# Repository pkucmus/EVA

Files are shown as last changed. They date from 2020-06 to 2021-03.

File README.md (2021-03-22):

# EVA 1 is deprecated since 2020-12-31 
# go to [EVA 2](https://main.eva-3d.page/) for the new thing

# EVA MGN Carriage Platform

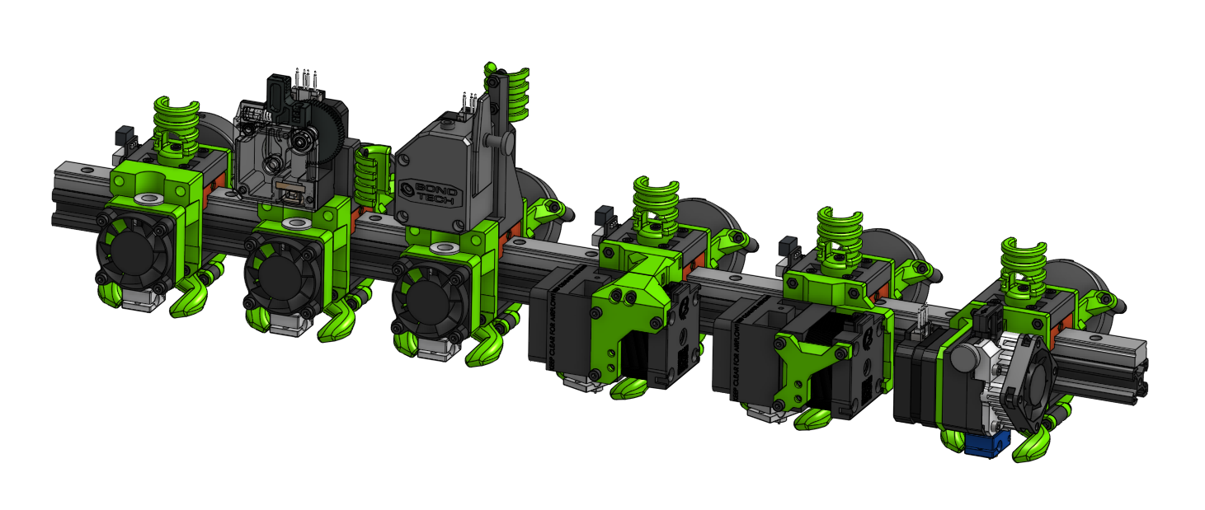
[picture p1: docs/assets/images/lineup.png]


I present to you the EVA carriage platform - easy to mount, remix and use MGN carriages for different Hotend assemblies.

They work great with the [Rat Rig V-core Pro](https://www.ratrig.com/3d-printing-cnc/3d-printer-kits/complete-kits/rat-rig-v-core-pro-linear-rail-701.html) "Easy mod" I created: https://github.com/pkucmus/Easy-Mod

A rather poor attempt to talk about those: https://www.youtube.com/playlist?list=PLR8LTCniA766Mg1a88iF8xhOlvZR-Rc3A

## Instructions

Visit the [project page](https://pkucmus.github.io/EVA/) for instructions and more information.

## Contribution

If you want to help with testing - please grab a carriage and report your findings as an [issue](https://github.com/pkucmus/EVA/issues) - please include pictures, videos and your opinion.

If you see anything missing from the Instructions - please file an [issue](https://github.com/pkucmus/EVA/issues).

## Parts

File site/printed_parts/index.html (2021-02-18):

Part | Link
bottom_mgn15_short_duct | GitHub (https://github.com/pkucmus/EVA/tree/master/docs/media/stls/bottom_mgn15_short_duct.stl)
Duct v2 Straight Risen | GitHub (https://github.com/pkucmus/EVA/tree/master/docs/media/stls/duct-v2-straight-risen.stl)
back_corexy_90deg | GitHub (https://github.com/pkucmus/EVA/tree/master/docs/media/stls/back_corexy_90deg.stl)
tension_slider_9mm_belt_M5_mirror | GitHub (https://github.com/pkucmus/EVA/tree/master/docs/media/stls/tension_slider_9mm_belt_m5_mirror.stl)
tension_slider_9mm_belt_M5 | GitHub (https://github.com/pkucmus/EVA/tree/master/docs/media/stls/tension_slider_9mm_belt_m5.stl)
cable_side | GitHub (https://github.com/pkucmus/EVA/tree/master/docs/media/stls/cable_side.stl)
unversal_cable_mount | GitHub (https://github.com/pkucmus/EVA/tree/master/docs/media/stls/unversal_cable_mount.stl)
top_mgn15_raw | GitHub (https://github.com/pkucmus/EVA/tree/master/docs/media/stls/top_mgn15_raw.stl)
face_v6 | GitHub (https://github.com/pkucmus/EVA/tree/master/docs/media/stls/face_v6.stl)
face_v6_40mm_fan | GitHub (https://github.com/pkucmus/EVA/tree/master/docs/media/stls/face_v6_40mm_fan.stl)
face_mosquito | GitHub (https://github.com/pkucmus/EVA/tree/master/docs/media/stls/face_mosquito.stl)
mosquito_front | GitHub (https://github.com/pkucmus/EVA/tree/master/docs/media/stls/mosquito_front.stl)
back_cartesian | GitHub (https://github.com/pkucmus/EVA/tree/master/docs/media/stls/back_cartesian.stl)
tension_slider_6mm_belt_M3 | GitHub (https://github.com/pkucmus/EVA/tree/master/docs/media/stls/tension_slider_6mm_belt_m3.stl)
cartesian_cable_fin | GitHub (https://github.com/pkucmus/EVA/tree/master/docs/media/stls/cartesian_cable_fin.stl)
bottom_mgn12_short_duct | GitHub (https://github.com/pkucmus/EVA/tree/master/docs/media/stls/bottom_mgn12_short_duct.stl)
top_mgn12_raw | GitHub (https://github.com/pkucmus/EVA/tree/master/docs/media/stls/top_mgn12_raw.stl)
face_titan | GitHub (https://github.com/pkucmus/EVA/tree/master/docs/media/stls/face_titan.stl)
face_mosquito_titan | GitHub (https://github.com/pkucmus/EVA/tree/master/docs/media/stls/face_mosquito_titan.stl)
top_mgn15_bmg | GitHub (https://github.com/pkucmus/EVA/tree/master/docs/media/stls/top_mgn15_bmg.stl)
top_mgn12_bmg | GitHub (https://github.com/pkucmus/EVA/tree/master/docs/media/stls/top_mgn12_bmg.stl)
bottom_mgn15_long_duct | GitHub (https://github.com/pkucmus/EVA/tree/master/docs/media/stls/bottom_mgn15_long_duct.stl)
face_aero | GitHub (https://github.com/pkucmus/EVA/tree/master/docs/media/stls/face_aero.stl)
face_aero_support | GitHub (https://github.com/pkucmus/EVA/tree/master/docs/media/stls/face_aero_support.stl)
bottom_mgn12_long_duct | GitHub (https://github.com/pkucmus/EVA/tree/master/docs/media/stls/bottom_mgn12_long_duct.stl)
Duct v2 Angled 20deg Risen | GitHub (https://github.com/pkucmus/EVA/tree/master/docs/media/stls/duct-v2-angled-20deg-risen.stl)
face_hemera | GitHub (https://github.com/pkucmus/EVA/tree/master/docs/media/stls/face_hemera.stl)
face_hemera_front | GitHub (https://github.com/pkucmus/EVA/tree/master/docs/media/stls/face_hemera_front.stl)
Duct v2 Volcano Straight Risen | GitHub (https://github.com/pkucmus/EVA/tree/master/docs/media/stls/Duct_v2_Volcano_Configurable_-_Duct_v2_Volcano_Straight_Risen.stl)
Duct v2 Volcano Angled Risen | GitHub (https://github.com/pkucmus/EVA/tree/master/docs/media/stls/Duct_v2_Volcano_Configurable_-_Duct_v2_Volcano_Angled_20deg_Risen.stl)
Back IDEX X1 | GitHub (https://github.com/pkucmus/EVA/tree/master/docs/media/stls/Back_IDEX_-_back_idex_x1.stl)
Back IDEX X2 | GitHub (https://github.com/pkucmus/EVA/tree/master/docs/media/stls/Back_IDEX_-_back_idex_x2.stl)

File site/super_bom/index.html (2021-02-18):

Name | Qty | Type | Link
bottom_mgn15_short_duct | 1.0 | printed | GitHub (https://github.com/pkucmus/EVA/tree/master/docs/media/stls/bottom_mgn15_short_duct.stl)
DIN 912 M3 20 mm | 5.0 | hardware
Duct v2 Straight Risen | 1.0 | printed | GitHub (https://github.com/pkucmus/EVA/tree/master/docs/media/stls/duct-v2-straight-risen.stl)
M3 Hex nut | 20.0 | hardware
back_corexy_90deg | 1.0 | printed | GitHub (https://github.com/pkucmus/EVA/tree/master/docs/media/stls/back_corexy_90deg.stl)
DIN 912 M5 35 mm | 2.0 | hardware
tension_slider_9mm_belt_M5_mirror | 1.0 | printed | GitHub (https://github.com/pkucmus/EVA/tree/master/docs/media/stls/tension_slider_9mm_belt_m5_mirror.stl)
tension_slider_9mm_belt_M5 | 1.0 | printed | GitHub (https://github.com/pkucmus/EVA/tree/master/docs/media/stls/tension_slider_9mm_belt_m5.stl)
5015 fan | 1.0 | hardware
M5 Hex nut | 2.0 | hardware
cable_side | 1.0 | printed | GitHub (https://github.com/pkucmus/EVA/tree/master/docs/media/stls/cable_side.stl)
unversal_cable_mount | 1.0 | printed | GitHub (https://github.com/pkucmus/EVA/tree/master/docs/media/stls/unversal_cable_mount.stl)
DIN 912 M3 10 mm | 10.0 | hardware
DIN 912 M3 12 mm | 9.0 | hardware
top_mgn15_raw | 1.0 | printed | GitHub (https://github.com/pkucmus/EVA/tree/master/docs/media/stls/top_mgn15_raw.stl)
face_v6 | 1.0 | printed | GitHub (https://github.com/pkucmus/EVA/tree/master/docs/media/stls/face_v6.stl)
DIN 912 M3 40 mm | 4.0 | hardware
face_v6_40mm_fan | 1.0 | printed | GitHub (https://github.com/pkucmus/EVA/tree/master/docs/media/stls/face_v6_40mm_fan.stl)
4010 FAN | 1.0 | hardware
V6-175-SINK | 1.0 | hardware
V6-300-BREAK | 1.0 | hardware
V6-BLOCK-CARTRIDGE | 1.0 | hardware
V6-NOZZLE-ALL | 1.0 | hardware
SOCK | 1.0 | hardware
DIN 912 M3 35 mm | 7.0 | hardware
mosquito | 1.0 | hardware
25mm fan | 1.0 | hardware
DIN 912 M3 25 mm | 3.0 | hardware
DIN 912 M2.5 12 mm | 2.0 | hardware
face_mosquito | 1.0 | printed | GitHub (https://github.com/pkucmus/EVA/tree/master/docs/media/stls/face_mosquito.stl)
mosquito_front | 1.0 | printed | GitHub (https://github.com/pkucmus/EVA/tree/master/docs/media/stls/mosquito_front.stl)
back_cartesian | 1.0 | printed | GitHub (https://github.com/pkucmus/EVA/tree/master/docs/media/stls/back_cartesian.stl)
tension_slider_6mm_belt_M3 | 1.0 | printed | GitHub (https://github.com/pkucmus/EVA/tree/master/docs/media/stls/tension_slider_6mm_belt_m3.stl)
cartesian_cable_fin | 1.0 | printed | GitHub (https://github.com/pkucmus/EVA/tree/master/docs/media/stls/cartesian_cable_fin.stl)
DIN 912 M3 30 mm | 2.0 | hardware
bottom_mgn12_short_duct | 1.0 | printed | GitHub (https://github.com/pkucmus/EVA/tree/master/docs/media/stls/bottom_mgn12_short_duct.stl)
DIN 912 M3 16 mm | 2.0 | hardware
top_mgn12_raw | 1.0 | printed | GitHub (https://github.com/pkucmus/EVA/tree/master/docs/media/stls/top_mgn12_raw.stl)
face_titan | 1.0 | printed | GitHub (https://github.com/pkucmus/EVA/tree/master/docs/media/stls/face_titan.stl)
PTFE Tube 73.6 millimeter | 1.0 | hardware
PTFE Tube 57 millimeter | 1.0 | hardware
face_mosquito_titan | 1.0 | printed | GitHub (https://github.com/pkucmus/EVA/tree/master/docs/media/stls/face_mosquito_titan.stl)
top_mgn15_bmg | 1.0 | printed | GitHub (https://github.com/pkucmus/EVA/tree/master/docs/media/stls/top_mgn15_bmg.stl)
BMG-M_Extruder | 1.0 | hardware
top_mgn12_bmg | 1.0 | printed | GitHub (https://github.com/pkucmus/EVA/tree/master/docs/media/stls/top_mgn12_bmg.stl)
bottom_mgn15_long_duct | 1.0 | printed | GitHub (https://github.com/pkucmus/EVA/tree/master/docs/media/stls/bottom_mgn15_long_duct.stl)
face_aero | 1.0 | printed | GitHub (https://github.com/pkucmus/EVA/tree/master/docs/media/stls/face_aero.stl)
face_aero_support | 1.0 | printed | GitHub (https://github.com/pkucmus/EVA/tree/master/docs/media/stls/face_aero_support.stl)
DIN 912 M3 8 mm | 5.0 | hardware
E3Dv6 Break | 1.0 | hardware
E3Dv6 Block | 1.0 | hardware
E3Dv6 Nozzle 0.4 | 1.0 | hardware
bottom_mgn12_long_duct | 1.0 | printed | GitHub (https://github.com/pkucmus/EVA/tree/master/docs/media/stls/bottom_mgn12_long_duct.stl)
Duct v2 Angled 20deg Risen | 1.0 | printed | GitHub (https://github.com/pkucmus/EVA/tree/master/docs/media/stls/duct-v2-angled-20deg-risen.stl)
40x40x10 DC Fan | 1.0 | hardware
HEMERA-175-SINK_1_1_1_1 | 1.0 | hardware
HEMERA-MOTOR_1_1_1_1_1_1 | 2.0 | hardware
V6-BLOCK-CARTRIDGE_1_1_1_1_1_1 | 1.0 | hardware
V6-NOZZLE_1_1_1_1_1_1 | 1.0 | hardware
HEMERA-175-BREAK_1_1_1_1_1_1 | 1.0 | hardware
square nut thin grade b_din_Square nut DIN 562 M3 -N_1_1_1_1_1 | 5.0 | hardware
face_hemera | 1.0 | printed | GitHub (https://github.com/pkucmus/EVA/tree/master/docs/media/stls/face_hemera.stl)
face_hemera_front | 1.0 | printed | GitHub (https://github.com/pkucmus/EVA/tree/master/docs/media/stls/face_hemera_front.stl)

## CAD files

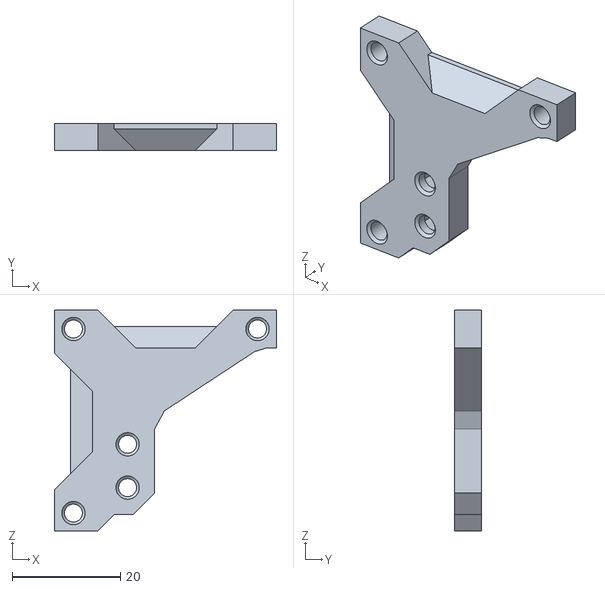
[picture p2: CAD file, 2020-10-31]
docs/media/stls/face_hemera_front.stl
41.0 x 5.00 x 40.8

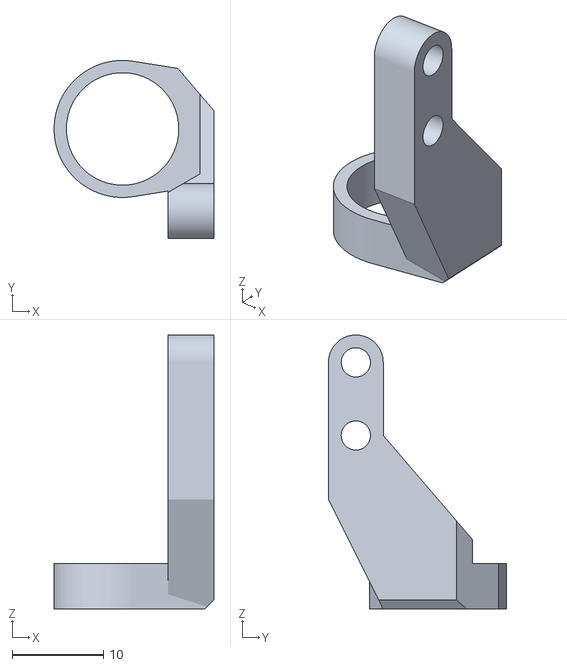
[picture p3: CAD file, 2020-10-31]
site/media/stls/probes - lj12_probe_left.stl
17.5 x 19.5 x 30.0

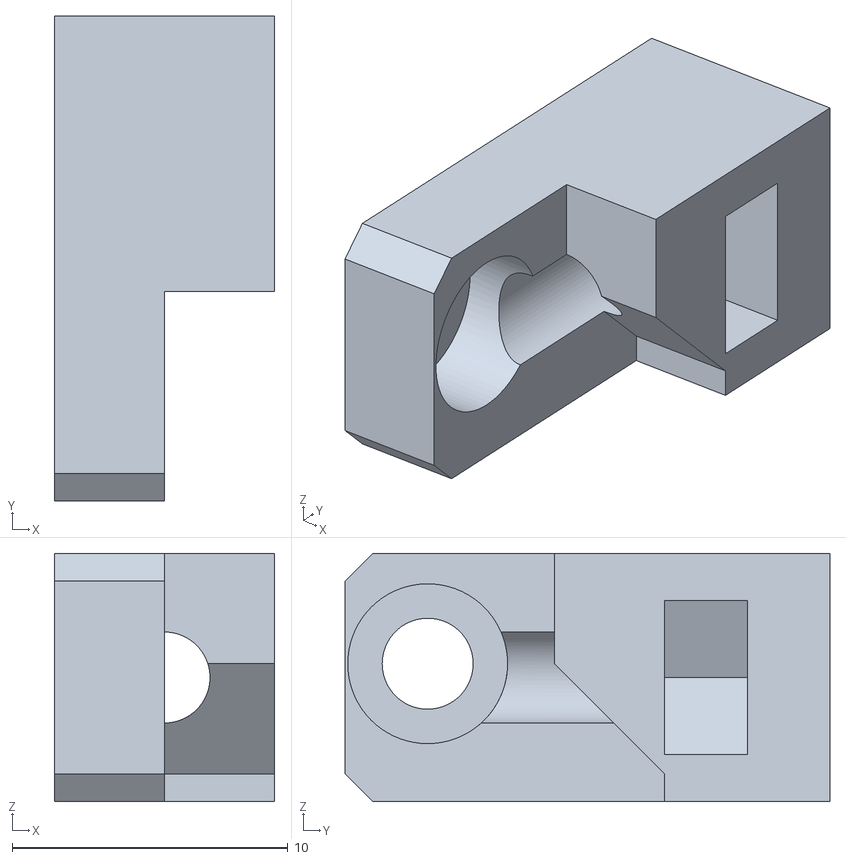
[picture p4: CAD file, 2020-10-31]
docs/media/stls/face_aero_support.stl
8.00 x 17.6 x 9.00

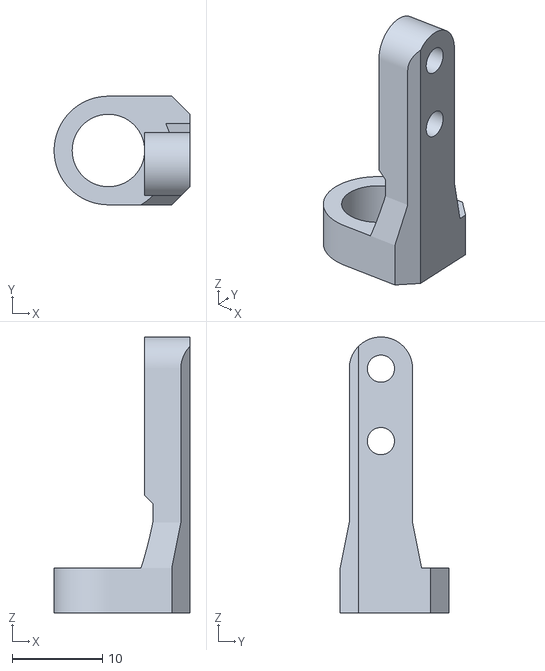
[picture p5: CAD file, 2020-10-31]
site/media/stls/probes - lj8_probe_center.stl
15.0 x 12.0 x 30.5

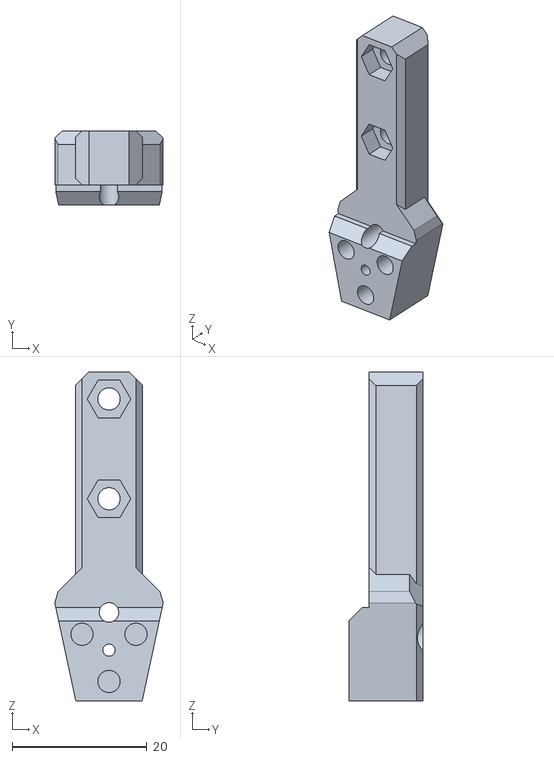
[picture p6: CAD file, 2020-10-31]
docs/media/stls/unversal_cable_mount.stl
16.1 x 11.0 x 48.8

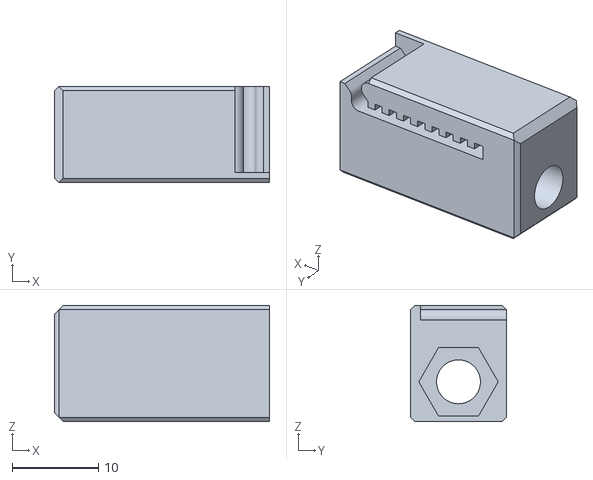
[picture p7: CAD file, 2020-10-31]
site/media/stls/tension sliders - tension_slider_9mm_belt_M5_mirror.stl
25.0 x 11.2 x 13.5

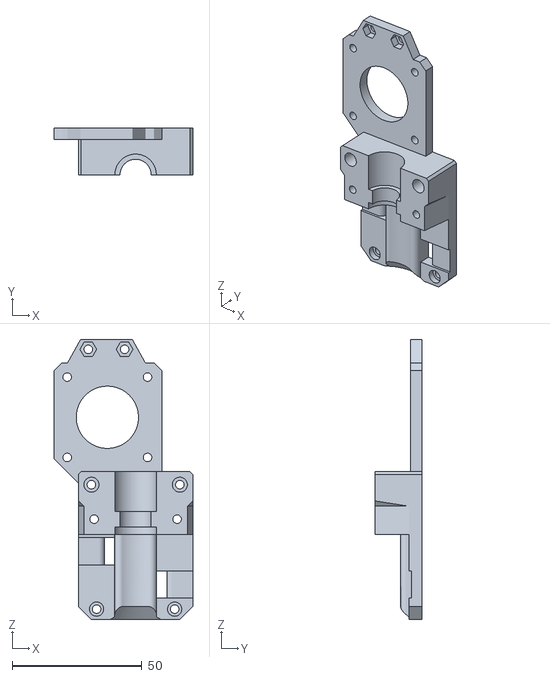
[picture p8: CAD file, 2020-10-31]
docs/media/stls/face_titan.stl
53.5 x 18.0 x 108.0

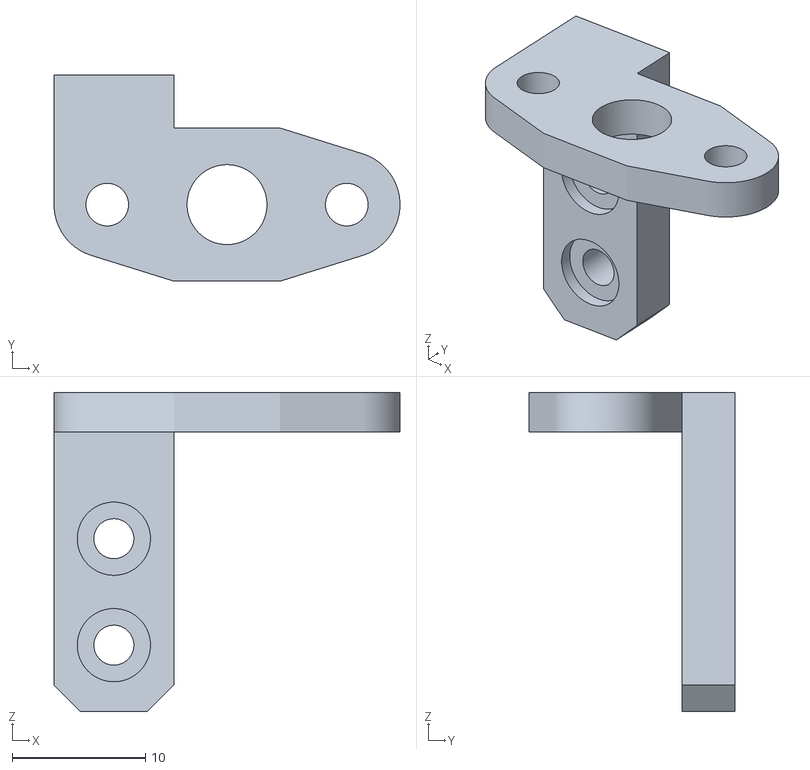
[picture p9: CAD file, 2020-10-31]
site/media/stls/probes - bl_touch_3mm.stl
26.0 x 15.5 x 24.0

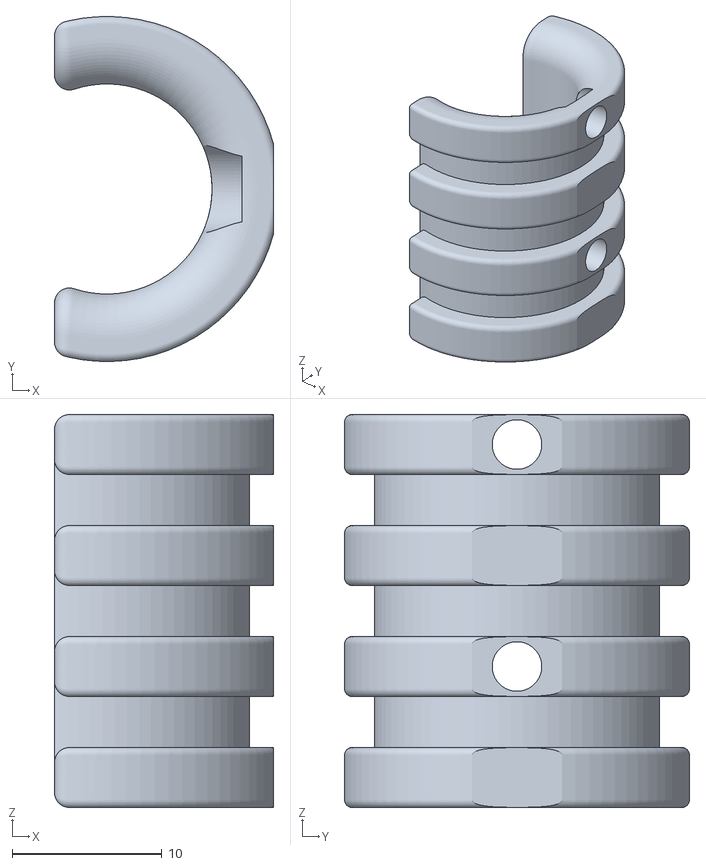
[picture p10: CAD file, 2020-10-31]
docs/media/stls/cable_side.stl
14.6 x 23.0 x 26.2

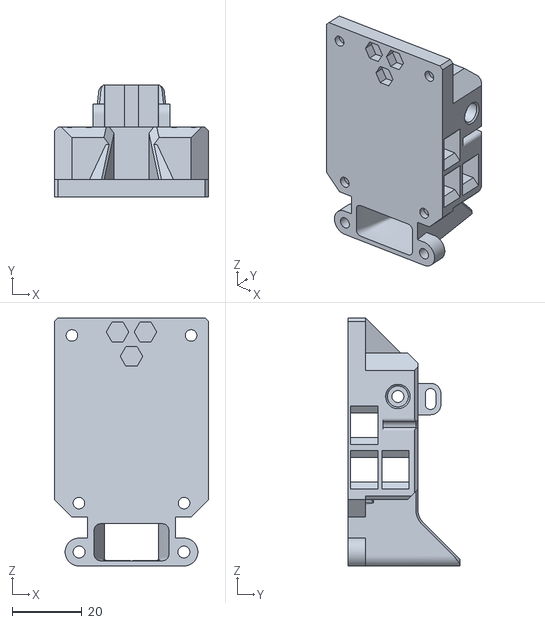
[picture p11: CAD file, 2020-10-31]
site/media/stls/Back_IDEX_-_back_idex_x2.stl
44.1 x 32.0 x 71.0

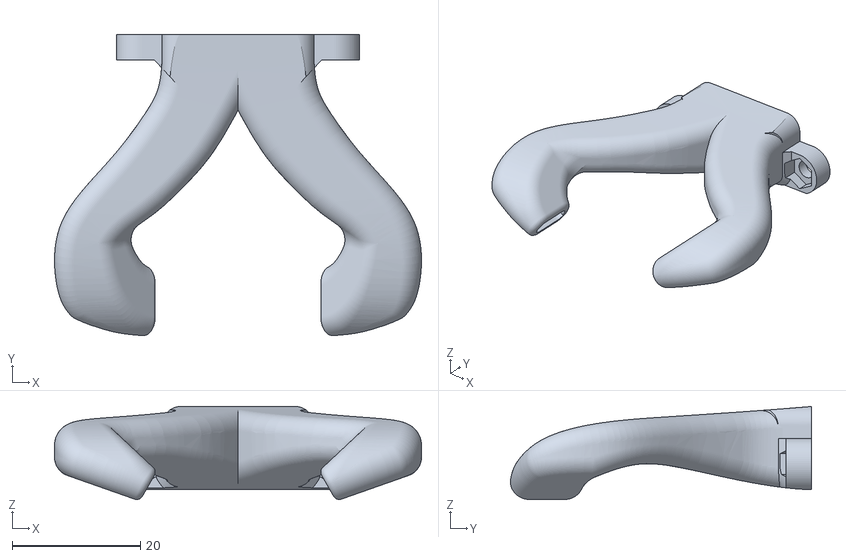
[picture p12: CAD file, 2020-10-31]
docs/media/stls/duct-v2-straight-risen.stl
57.3 x 47.0 x 14.5

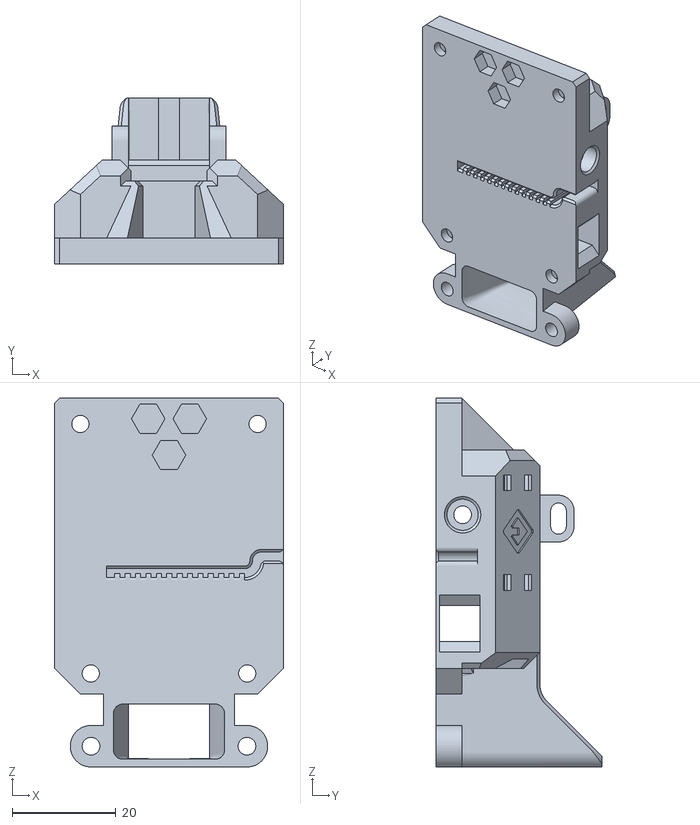
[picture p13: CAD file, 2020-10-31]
docs/media/stls/back_cartesian.stl
44.1 x 32.0 x 71.0

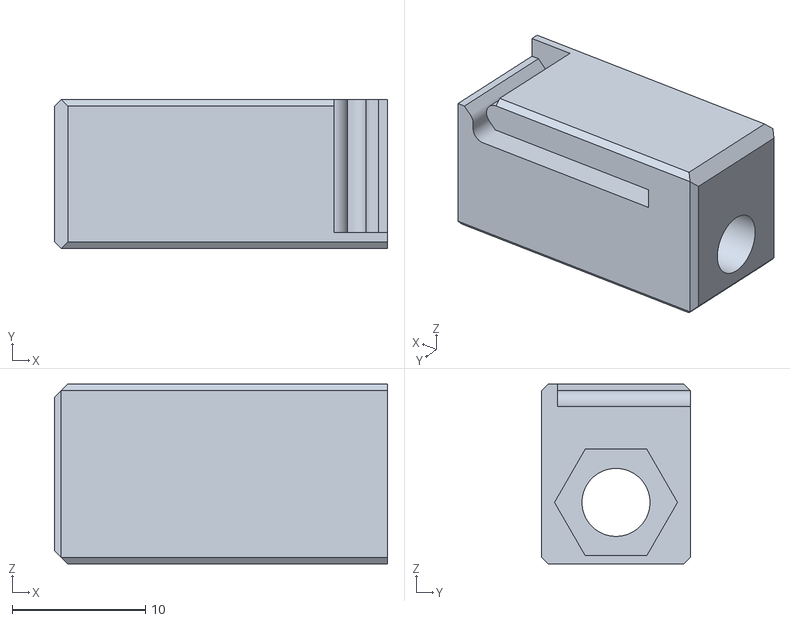
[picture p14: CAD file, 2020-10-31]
site/media/stls/tension sliders - tension_slider_9mm_belt_M5_flip_mirror.stl
25.0 x 11.2 x 13.5

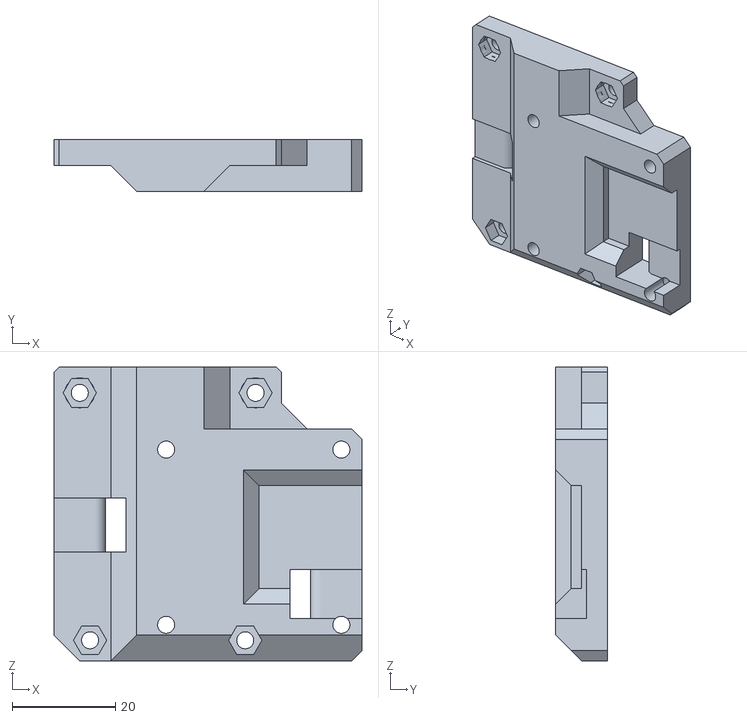
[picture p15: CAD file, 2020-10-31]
docs/media/stls/face_hemera.stl
59.8 x 10.0 x 57.0

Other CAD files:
site/media/stls/tension sliders - tension_slider_9mm_belt_M5.stl
site/media/stls/Back_IDEX_-_back_idex_x1.stl
docs/media/stls/bottom_mgn15_long_duct.stl
site/media/stls/probes - lj8_probe_right.stl
docs/media/stls/back_corexy_90deg.stl
docs/media/stls/bottom_mgn12_long_duct.stl
docs/media/stls/bottom_mgn12_short_duct.stl
docs/media/stls/bottom_mgn15_short_duct.stl
docs/media/stls/cartesian_cable_fin.stl
docs/media/stls/duct-v2-angled-20deg-risen.stl
docs/media/stls/face_aero.stl
docs/media/stls/face_mosquito.stl
docs/media/stls/face_mosquito_titan.stl
docs/media/stls/face_v6.stl
docs/media/stls/face_v6_40mm_fan.stl
docs/media/stls/mosquito_front.stl
docs/media/stls/tension_slider_6mm_belt_m3.stl
docs/media/stls/tension_slider_9mm_belt_m5.stl
docs/media/stls/tension_slider_9mm_belt_m5_mirror.stl
docs/media/stls/top_mgn12_bmg.stl
docs/media/stls/top_mgn12_raw.stl
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

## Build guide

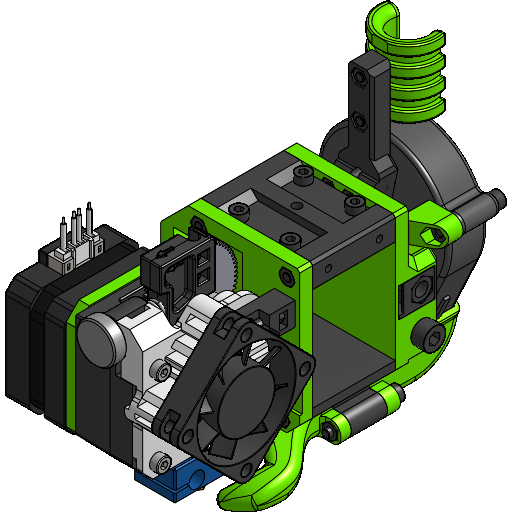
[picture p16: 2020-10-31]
site/media/assemblies/44f6d805bfa7d15742b3ac6fList_SNSHSCw9hkRS4VDefaultList_AYF7J5g18MUh8SDefault.png

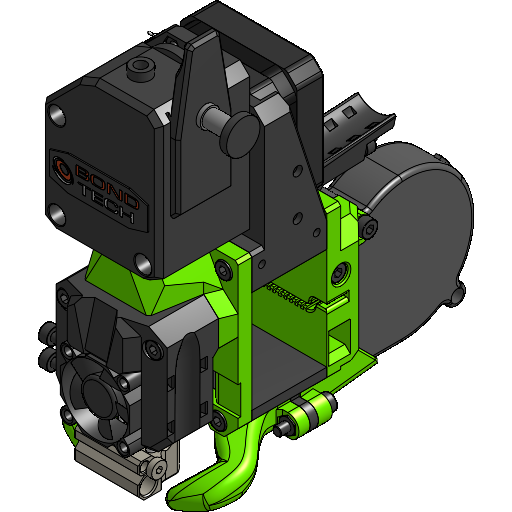
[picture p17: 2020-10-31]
docs/media/assemblies/e089ef52b1a648887b30ed21List_tcI8zlLYtHoV29MGN12List_6rEL4KZ3PThss0MosquitoLi_g8Y7Tob.png

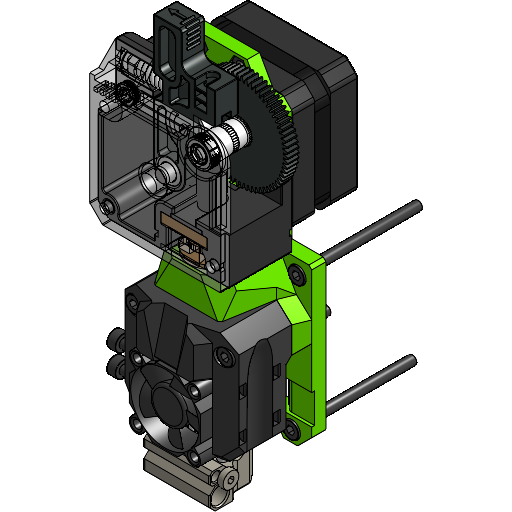
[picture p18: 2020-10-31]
docs/media/sub_assemblies/Face_Mosquito_Titan.png

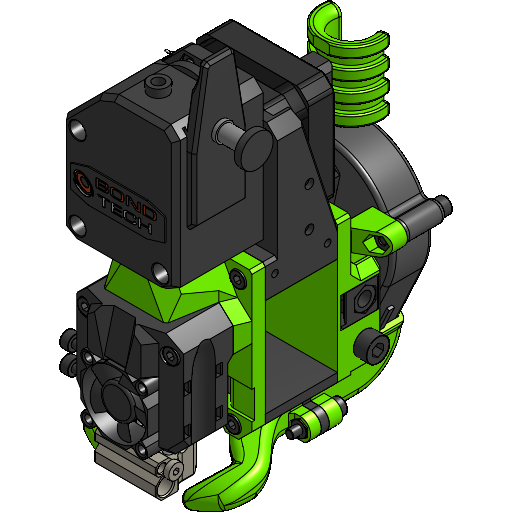
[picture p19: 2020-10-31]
docs/media/assemblies/e089ef52b1a648887b30ed21List_tcI8zlLYtHoV29MGN12List_6rEL4KZ3PThss0Mosquito_B_u0amaoS.png

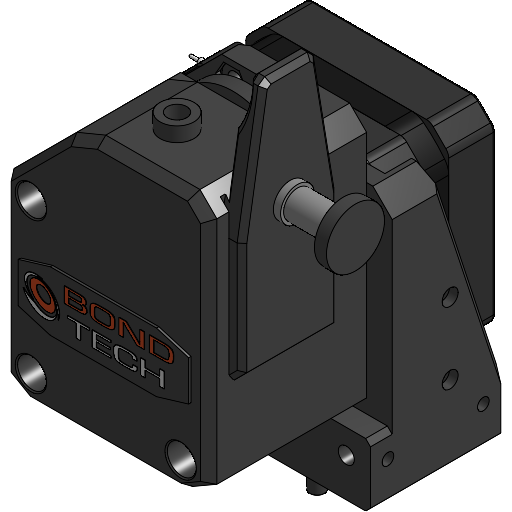
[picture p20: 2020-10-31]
site/media/sub_assemblies/Top_BMG_XyYwNrb.png

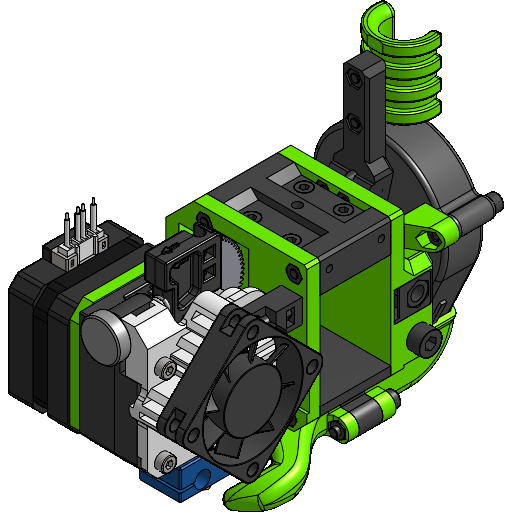
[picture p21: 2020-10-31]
docs/media/assemblies/44f6d805bfa7d15742b3ac6fList_SNSHSCw9hkRS4VMGN12List_AYF7J5g18MUh8SDefault.png

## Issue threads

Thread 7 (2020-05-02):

Anycubic / Creality Cartesian Mods

DavaD85, 2020-05-02:
Hi
I would like to know if is possible to have a simple mod to fit this Extruder to a cartesian printer like Chiron or Cr10, I need to have a single belt.

Thanks!

pkucmus, 2020-05-02:
We talked and there is a difficulty coming out from the belt issue CR-10 and it's derivatives has. Additionally there is not much space on the back for an EVA back belt mount.

Ideas are welcome :)

pkucmus, 2020-05-07:
I have a cartesian version in the workings but it will require a change in the belt paths on the CR-10 deriatives

pkucmus, 2020-05-10:
The cartesian version of EVA is uploaded, more information here: https://pkucmus.github.io/EVA/sub_assemblies/cartesian_back/

pkucmus, 2020-06-06:
Cartesian back is available. Different mods for different printers would need to be done as mods for those printers. There's also V-cast incoming: https://www.ratrig.com/3d-printing-cnc/3d-printer-kits/complete-kits/rat-rig-v-cast.html

Closed 2020-06-06.

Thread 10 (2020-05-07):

fandduck its lower than the nozzle

DavaD85, 2020-05-07:
I tried to print the fanduck and it's lower than the nozzle, maybe it's the abs retraction during the print of this part, it's possible to move up a little?
Thanks

DavaD85, 2020-05-07:
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

pkucmus, 2020-05-07:
I'm going to pause on this one to make sure it's not a printout issue.

pkucmus, 2020-05-27:
Do I recall correctly that we talked about it on Messenger and the issue is resolved?

PeterDavidsson, 2020-05-28:
Hi,
I do also have this problem, how did you solve this?
I have tride both versions of your horn_duct.

pkucmus, 2020-05-28:
I suppose this might be an issue with different sizes of heat blocks - there seems to be two. I guess I'll need to make one that's 2mm(?) raised.

PeterDavidsson, 2020-05-29:
That would be nice.
I also hade to remove the bottomplate distance were you mount the shroud to make airflow spot on.
But 2mm higher would be very nice.

pkucmus, 2020-05-29:
Please tell me what exactly do you mean by "remove the bottomplate distance" ?

pkucmus, 2020-05-29:
I uploaded raised versions to a test branch: https://github.com/pkucmus/EVA/tree/raised_duct/stl (look for `_raised` files - it's raised 1mm (2mm seemed too much).

Please let me know if it's better so I can release it officially.

PeterDavidsson, 2020-06-02:
now the flow is spot on for me
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

pkucmus, 2020-06-06:
Fixed with 1.1.0

Closed 2020-06-06.

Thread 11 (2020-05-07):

Belt tension for sapphire plus

DavaD85, 2020-05-07:
Hi
My Sapphire plus have the belts in the opposite side and I need to mirror this part, it's possible?
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
![Uploading 20200507_222611.jpg…]()

DavaD85, 2020-05-07:
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

pkucmus, 2020-05-07:
Since we started talking about it outside of GitHub it's already done :D

https://github.com/pkucmus/EVA/blob/flipped_slider/stl/Dynamic%20-%20Slider.stl

Please let me know if it works.

DavaD85, 2020-05-08:
Hi
As you can see I need to move the belt a little
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
And the part is a little lower than the original

pkucmus, 2020-05-27:
I think we talked about it. Two things can be done here:
1. Thicken the back part to offset the belt tensioner
2. Change the XY joiner part of the printer

I'd rather opt for the later one, since there's already little space in Y on that printer.

pkucmus, 2020-06-06:
Different belt tension sliders are now available - fill support for Sapphire plus is not something I can take on. Closing this one :)

Closed 2020-06-06.

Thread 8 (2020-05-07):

Mount for BMG Aero

KipK, 2020-05-07:
Hi

Great work you did here.

I've started to make a mount for the new BMG Aero from mellow. It' a kind of a remix of a BMG with Hemera heatsink, the titan aero way.

https://www.aliexpress.com/i/4000084805415.html

I'd like to remix your fan duct on it, would you mind to share the step file ?

Thanks

Gui

pkucmus, 2020-05-07:
Thank you and Awesome! You'd like it to be a part of EVA?

The thing is that I can't guarantee that stuff will not change at this point but if you still want to give it a go I could give you the required step files (the ducts and a base face maybe?).

KipK, 2020-05-07:
Sure, whatever you have that can inspire me too. If you have the Hemera
step file too as booth have almost the same footprint

I'm almost done making a BLV mount for it that fits bltouch and 5015 blower
but I'm now stuck fitting a proper cooling duct.
I don't mind redoing it by to be more EVA lookish ;)
How the fan ducts doing is job on your setup?
I was quiet used to double 4010 blowers.

Le jeu. 7 mai 2020 à 17:21, Paweł Kucmus <notifications@github.com> a
écrit :

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

KipK, 2020-05-07:
Titan aero mount seems the nearest start  for this one. So I'd rather have this step
Here is a STL of the extruder
https://www.thingiverse.com/thing:4226245

pkucmus, 2020-05-08:
To answer the question about he fan duct - it's doing very well, I was surprised i.e. how long of a bridge I can make with it.
Here's a CFG simulation result from this week:
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

pkucmus, 2020-05-27:
Ho is it going? Do you need anything else?

KipK, 2020-05-30:
Hey.

Sorry was busy those days.
I've misthought it was for BLV mgn printer.
Tryed to modify for it and fits all my needs but finally was not satisfied
by this extruder positioning and weight. ( Not your design but this
extruder design sideways as I prefer a dual blower config.
For now I've made something else, but will probably work on it back later

Le mer. 27 mai 2020 à 09:41, Paweł Kucmus <notifications@github.com> a
écrit :

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

pkucmus, 2020-09-05:
Thanks, I'll close this one for now, we can always revisit the idea in the future

Closed 2020-09-05.

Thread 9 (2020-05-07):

fan problem

DavaD85, 2020-05-07:
I need to move a little down the back fan because doesn't fit in my Sapphire plus frame.

DavaD85, 2020-05-07:
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

pkucmus, 2020-05-09:
I made 4 more versions which total up to 5:
* 30 deg
* 45 deg
* 60 deg (default)
* 80 deg
* 90 deg

And I will upload those tomorrow.

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

DavaD85, 2020-05-10:
Did you have time to upload these stl?

pkucmus, 2020-05-10:
5 different angles are now available: https://pkucmus.github.io/EVA/sub_assemblies/core_xy_back/ also for cartesians https://pkucmus.github.io/EVA/sub_assemblies/cartesian_back/.

Please yet me know here if you are happy with them.

pkucmus, 2020-05-27:
Closing the request as resolved. Let me know if you need anything else.

Closed 2020-05-27.

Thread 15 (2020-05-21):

Requested highier tolerance

pkucmus, 2020-05-21:
Following issues where reported to me:

1. a little more tolerance on tensioner parts is needed
2. screw holes should be a bit bigger - not to thread into the plastic
3. a square nut tensioner block variant for the cartesian back was requested
4. a shorter channel for the nut

pkucmus, 2020-06-06:
Fixed with 1.1.0

Closed 2020-06-06.

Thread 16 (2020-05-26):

Inductive probes with horn duct conflict

M1dn1ghtN1nj4, 2020-05-26:
For the setup I'm looking to put together, there seems to be a problem with the both the 8mm and 12mm inductive bed probes with the horn duct.  Or could it be that I'm somehow not assembling this right.  The photos show it like it fits, but I can't find a combination that works.

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

pkucmus, 2020-05-27:
You are probably looking for the "_right" variants of the probes.
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
All probe holder variants are here: https://github.com/pkucmus/EVA/tree/master/stl/Probe%20Mounts

Please let me know if that helps.

pkucmus, 2020-05-29:
Any updates?

M1dn1ghtN1nj4, 2020-05-29:
Yep, that works.  I picked the left side one because it brings the probe more in line with the nozzle.  It's how I've designed all of my printers.  The probe and nozzle are perfectly in line in the Y axis.  Just a bit OCD on my part.  I also had to shorten up the horn duct a little.  The output was about 4mm to 5mm ahead of the nozzle tip.
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

pkucmus, 2020-05-29:
Alright, thanks for the update! Issue resolved then?

M1dn1ghtN1nj4, 2020-05-30:
Yep.  All good!  Thanks

Closed 2020-05-30.

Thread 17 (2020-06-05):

Requested Mosquito/Nf-Crazy Mount

morpheus200, 2020-06-05:
Request for Mosquito or NF-Crazy (Clone) Hotend. The Hotend is almost compatible with the V6, the differences are very small.

pkucmus, 2020-06-05:
There are people trying to organize those for me so that I can measure, design and test - so it's coming, but has no ETA yet.

joaobarros, 2020-06-18:
Plus one on this request, let me know if you need anything

pkucmus, 2020-06-18:
I should get a Mosquito soon (I hope) I'll start the work then.

maziggy, 2020-10-12:
+1

pkucmus, 2020-10-13:
Those are ready to be tested, once I'll do my testing I'll release, you can try to use the current version but stuff may change. Also If you'll use please share your feedback: https://cad.onshape.com/documents/1cea28d26150bba34a3d6614/w/fd185c58d38d06bda7ec83a6/e/180aabbd13bbeefb972e31a1
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

EduardoOliveira, 2020-10-13:
The fan face looks awesome

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

maziggy, 2020-10-14:
> Those are ready to be tested, once I'll do my testing I'll release, you can try to use the current version but stuff may change.

Where can I find it?

pkucmus, 2020-10-18:
Please check out the unified BMG/BMG-M approach that also gets rid of the groove mount adapter requirement. Thanks miklschmidt!
https://cad.onshape.com/documents/1cea28d26150bba34a3d6614/w/fd185c58d38d06bda7ec83a6/e/db5e779d6e295e18e56f51d3

miklschmidt, 2020-10-18:
Muuuch better! 👍

maziggy, 2020-10-18:
When using a BMG-M I don't see any advantage compared to the design before?

miklschmidt, 2020-10-18:
@maziggy There's no real benefit to the BMG-M version unless the mosquito is mounted directly to the extruder (shorter filament travel path). As far as i can tell, that's not possible in the current EVA design.

pkucmus, 2020-10-18:
EVA is much about supporting what people may have on hand, if one is switching to EVA from a Mosquito with a BMG that BMG is likely a BMG-M, so we wanted EVA to support either one of those. This particular update makes me happy since in theory one set of those parts can support both permutations. I hope to have it tested soon.

maziggy, 2020-10-19:
Thanks, makes sense. I already printed the former version and will try it today.

maziggy, 2020-10-20:
Found a little issue. Printed all parts for a mgn12 carriage and found out that the front plate doesn't fit. The screw holes are to close to each other. It looks like the top_mgn15_bmg.stl fits to a mgn12h. Printing it while writing and let you know.

maziggy, 2020-10-20:
Just fount out that your model is for a mgn12c. I have a mgn12h. Will move the screw holes.

maziggy, 2020-10-25:
Will test it now. Assembling was no issue. Very nice design.
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

pkucmus, 2020-10-25:
1.4.0-RC2 carries newest improvements (still work in progress): https://cad.onshape.com/documents/1cea28d26150bba34a3d6614/v/93a8541e17dd938c15833def/e/db5e779d6e295e18e56f51d3

maziggy, 2020-10-26:
> Those are ready to be tested, once I'll do my testing I'll release, you can try to use the current version but stuff may change. Also If you'll use please share your feedback: https://cad.onshape.com/documents/1cea28d26150bba34a3d6614/w/fd185c58d38d06bda7ec83a6/e/180aabbd13bbeefb972e31a1
> 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

Are you aware of any filament path issues in this version? First print was successfull but after unloading the filament I was not able to load a new one. Filament was stuck at the end of the printed part diretly above the Mosquito. Cleared the path and again the first print was good but problems reoccured when changing filament.

miklschmidt, 2020-10-26:
@maziggy you should use a piece of bowden tube between the BMG and the Mosquito.

pkucmus, 2020-10-26:
Added some clearance to the PTFE hole, 1.4.0-RC3: https://cad.onshape.com/documents/1cea28d26150bba34a3d6614/v/630104b77ee640cfa5db0a31/e/1cca3cb2ad6c3a96d3e9486e

maziggy, 2020-10-28:
Thanks, works perfect.

pkucmus, 2020-11-01:
Mosquito support is now released in 1.4.0. Thanks for all the input!

maziggy, 2020-11-08:
Within the last few months I've tried mayn different designs for the combination Mosquito and Bondtech. Some good ones but nothing without any disadvantages. After printing now for two weeks with your design I can say that's the way to go for me. No issues at all.

To tell a long story short: no knick-knack, very easy to assemblle and it just works reliable as it should. Many thanks for your work!!!

Closed 2020-11-01.

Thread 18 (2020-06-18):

Mount request for Duet Mini IR led sensor 1.2

piksliviksi, 2020-06-18:
Hi!

Any chance of getting the mount for https://miscsolutions.wordpress.com/mini-height-sensor-board/ ?

pkucmus, 2020-06-18:
I think it should be possible. I don't know anything about it though. Saw some examples like: https://www.thingiverse.com/thing:939909. Is that something to aim for?

piksliviksi, 2020-06-18:
Yes, that's the thing.
It has to be 2.5-3mm higher than the nozzle from the buildplate. Other than that, it's a fairly simple pcb with 2 holes in it:
Top right corner (24.0, 17.62)
Mounting hole centres (2.70, 14.92) and (21.11, 14.92)
Mounting hole diameter 2.8
and the pcb thickness is 1.5mm and the total amount of space it takes is about 15mm, together with the components on the pcb.

joaobarros, 2020-12-10:
STEP model of the sensor from here: https://grabcad.com/library/dc42-mini-ir-height-sensor-1
[dc42-mini-ir-height-sensor-1.snapshot.2.zip](https://github.com/pkucmus/EVA/files/5674301/dc42-mini-ir-height-sensor-1.snapshot.2.zip)

The sensor bottom should be ~1.5mm higher relative to the nozzle as per documentation:

_"The bottom edge of the board should be no more than 2mm higher than the tip of the nozzle, to ensure that it will trigger before the nozzle touches the bed. To avoid the risk of the board fouling on the print, we suggest that the bottom edge is at least 1mm higher than the tip of the nozzle. So aim for 1.5mm."

Although a fixed position holder would be good as a start, an adjustable height holder would be great to be able to adjust to different bed surfaces.

pkucmus, 2020-12-31:
Moving to EVA 2

Closed 2020-12-31.

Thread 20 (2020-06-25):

Request for alternative belt fixation

morpheus200, 2020-06-25:
Could you provide a "old school" belt fixation with two holes and a zip for the backplate?

pkucmus, 2020-07-05:
One that would have no built-in tensioning?

morpheus200, 2020-07-05:
Yes without built-in tensioning, same as the frontplate.

pkucmus, 2020-08-28:
What we could do here is to make a tension slider that will behave in that manner, to be frank I really don't want to support another variant of the back :)

pkucmus, 2020-12-31:
Please move this Issue to EVA 2 https://github.com/EVA-3D/eva-main/issues if it's still something to desire :) (please also put the link to this issue there)

Closed 2020-12-31.

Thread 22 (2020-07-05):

Mirrored Bondtech BMG Top Mount

nexx, 2020-07-05:
As requested, I am opening this issue regarding mirroring the BMG top mount.

You may wish to mention in the documentation that the BMG Top can be mirrored to allow for use with the mirrored BMG extruders. I have tested this and can confirm everything lines up as expected.

Thanks for the fantastic work on the EVA design!

pkucmus, 2020-08-28:
Aaand I forgot to mention that in 1.3.0 :D There's probably some English to fix there so I'll add the info about this in one go.

pkucmus, 2020-08-29:
Applied to:
https://pkucmus.github.io/EVA/assemblies/v6_titan/ and https://pkucmus.github.io/EVA/assemblies/v6_bmg/
Thanks!

Closed 2020-08-29.

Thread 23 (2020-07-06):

XY joiner for HEVO

joaobarros, 2020-07-06:
There's a big potential crowd for the EVA system on current HEVO builds that want to move to rails.

A mod of your Easymod would allow for a "simple" migration to rails and the EVA

Some considerations about the differences of an HEVO and the Easymod on a V-Core Pro:
- 3030 vs 2040
- on the HEVO the belts run closer to the frames then on the V-Core Pro
-
- the Easymod uses the plates from the original V-Core Pro, the new XY joiner should be all printed to have dependencies on custom hardware

As we discussed this is a personal need/request but one that I have confidence would have a large amount of followers :)

pkucmus, 2020-07-15:
Are there any STEP files for an MGN HEVO I could use as reference?

joaobarros, 2020-07-15:
This project has a .f3d file: https://www.thingiverse.com/thing:4460475
If you are unable to open .f3d files I can export.

That project has 2 versions: full (XY) and half (just X), but I believe like myself, most people will go for the full version
Thank you for looking into this!

pkucmus, 2020-07-15:
Please export to STEP, thank you.

joaobarros, 2020-07-15:
Online model: https://bit.ly/393Kht4
STEP file with all the parts: https://www.dropbox.com/s/nnhjuvkw4zrp5u2/HEVO_3030_MGN_Rail_Conversion.step.zip?dl=0
Let me know if you prefer single objects STEPs

pkucmus, 2020-07-15:
This is great, thank you!

pkucmus, 2020-12-31:
Please move this Issue to EVA 2 https://github.com/EVA-3D/eva-main/issues if it's still something to desire :) (please also put the link to this issue there)

Closed 2020-12-31.

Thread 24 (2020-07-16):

Duet 3 Toolboard Support

philkry, 2020-07-16:
Amazing design you came up with, like it a lot!

For my new CoreXY printer i'm planning to make use of the new Duet 3 Toolboards (https://duet3d.dozuki.com/Wiki/Duet_3_Tool_Board) to reduce the number of cables running to my extruders.

Have you considered supporting it on your EVA platform?

It can be mounted onto a Hemera, so it can be used directly with only minor changes to Z probe mounts.
However for the other extruders, i'm unsure how to integrate it.

philkry, 2020-07-21:
Hey, i spent some time tweaking the V6 BMG version. It is not ideal yet and requires more tweaking as it sticks out to the side a bit too much.
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

pkucmus, 2020-07-21:
Nice. The drawback is that the motor size is limited now but I'm happy that you put work in to EVA. Thanks!

To say that EVA can support the tool board I would need to add that capability to all variants - not sure it's feasible.

philkry, 2020-07-21:
Yes, i was considering the stepper size as well, but thought when using a geared BMG extruder, you most likely will only require a pancake stepper rather than a full sized one. It would also make the overall assembly considerably more heavier.

I agree, its probably not really feasible to integrate it into all mounts, maybe using a Toolboard is even too niche but i thought i share this as i plan to build my new printer from scratch based on them (but i also only plan to use Hemera and V6 BMG).

I will post updates here in case someone else finds it useful.

pkucmus, 2020-07-21:
Awesome. Let me know when you are done and would like to be featured in EVA's documentation.

philkry, 2020-08-10:
so i did some changes to my initial design. i did move the mount to the side of the top module. this now allows all stepper sizes to be used, but more importantly, allows quicker changing the entire carriage.
with the toolboard mounted at the back (first iteration) you needed to disassemble the entire thing to get the motor out, which kinda defies the purpose of using a toolboard entirely.

you can find my version (mgn15 only for now) here https://github.com/philkry/EVA/blob/master/stl/Tops/top_MGN15_bmg_toolboard.stl

please note, it is still untested as i'm waiting for my printer to be delivered ;)

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

philkry, 2020-08-24:
@arsi-apli nice design!
just wondering, is there a reason why you did not just use the Hemera Alternative version of EVA? It would allow to mount the toolboard directly onto the front of Hemera, just the probe mount would need adjustment. that way you could stay as close to 'stock' EVA as possible.
dont get me wrong, it looks good, although more complicated than i think it needs to be.

pkucmus, 2020-08-24:
There are a few things to consider:
1. What is the benefit of having the tool head? Having it on a fixed Hemera carriage is just reducing the cables required from the main board to the carriage, right? Quite frankly it does not seem compelling. (more in point 3)
2. To be a part of the EVA platform a feature needs to work for all variants, the top part feels like a more proper or generic place to mount this.
3. Let's look into the crystal ball a little bit here: if EVA was to support tool changers, it would be a face with the locking mechanism that would grab a face that would hold a tool board, maybe? I don't know yet.

philkry, 2020-08-25:
> What is the benefit of having the tool head? Having it on a fixed Hemera carriage is just reducing the cables required from the main board to the carriage, right? Quite frankly it does not seem compelling. (more in point 3)

well, yes. the reduced amount of cables was my initial reason to opt for a toolboard. i like the EVA platform as it would allow me to reduce the efforts needed on manual changing the tool heads. less cables help here as the EVA carriage would be pretty much self-contained and you could just connect power + CAN bus.

on the other hand, you could achieve the same by crimping connectors to all cables (2 fans, thermistor, heater, probe) but that makes it bulky and not so easy to use again. if EVA ever makes it towards a tool changer system (your point 3) that point would even become obsolete as you would have the tools permanently connected.

were i still see benefits though, even on the long term is, that the tool board also provides you with an additional stepper driver for your extruder. you would not need extension boards anymore and could again achieve self-contained EVA carriages which contain everything you need for driving an extruder assembly.

> To be a part of the EVA platform a feature needs to work for all variants, the top part feels like a more proper or generic place to mount this.

good point! makes sense.

joaobarros, 2020-08-25:
I too am interested in this, the toolboards will become more mainstream as they will be supported in the upcoming Duet 3 Mini
High-end heaters and temp sensors come with short cables so board placement and thus distance is important, just wanted to point that what 😉

arsi-apli, 2020-08-25:
My opinion is that the toolboard helps to reduce vibrations. A common bundle of cables already weighs something, plus the load they exert on the printhead is not linear. That's the main reason I want to use it. And other benefits that have already been mentioned.

Unfortunately, there are belts by the sides and therefore I'm still thinking about putting the linear rail down and a flat cable for power supply and CAN Bus will be stored in the upper slot in the ALU profile with a short loop to the print head. The same mounting will be on the second axis.

pkucmus, 2020-08-25:
Thank you all for the valuable info. I like the idea of supporting the tool board (if that was not obvious).
I think we need to look at two permutations:
1. for the top free heads (bowden, aero, hemera) - the tool board flat on top which will not work best with the cable mounts coming in 1.3.0
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
philkry, 2020-10-04:
i just disassembled everything and double checked. and yes, i agree, the motor connector is dangerously close to the screw. i think i was just lucky with my particular toolboard.
maybe you can make the base a few millimeters thicker so there is a bit of a safty distance?

pkucmus, 2020-10-10:
As a FYI I think I'll move this out of EVA and put it one some "EVA extras" project, I'm trying to keep up with all the permutations and it's a chore. Any ideas for a better name than "EVA extras"?

philkry, 2020-10-12:
Guess EVA extras would be fine, other options would be 'EVA extensions' or 'EVA contrib' ?

EduardoOliveira, 2020-10-12:
I can see contrib for parts that are designed by other members and of which
you only have the step file, linking to external sources, and not
garanteing updates

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

pkucmus, 2020-10-12:
Someone suggested "EVA Addons" on Discord, I think that represents that those would be best. Toolboard addon is now in a separate document: https://cad.onshape.com/documents/255cffe335d549be4c0d4c52/w/027a43fe00d211ea4230f02e/e/821b45343fc77d009d4ac8c6 (still work in progress) but once I release everything will be described in main EVA docs

kuon, 2020-10-20:
But how will you "standardize" the addons mouting in the base EVA?

Should we consider those 5 holes "addon mount"? But what about variant without the top part (like BGM bowden)?

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

pkucmus, 2020-10-20:
The 3 hole mount would be a standard.
For the variants that have their tops free there's doing to be an angled tool board base (so the toolboard will be flat on top).
The "top heavy" ones get the 2 extra holes for the board base to grab by so that the tool board does not wobble like crazy on Y moves.

kuon, 2020-10-20:
So if we want to design other addons, we can rely on the 3 holes for variants with no top, and 5 holes for those with "heavy" top?

pkucmus, 2020-10-20:
I want to say "yes" but I will be more comfortable once I figure this one completely, the 3 holes are set in stone I think, the 2 top ones not so sure, and for the ones with clear top there's an opportunity for a screw or two as well
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

kuon, 2020-10-26:
The bracket for the BMG has a very thin wall (red line). I think it should be around 0.4-0.5mm for better printability.

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

joaobarros, 2020-10-29:
So I finally printed my Toolboard cover and I've got some issue, the major one being the extra height of a connector:

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

Then it's small details that are difficult to print and can eventually break off, as I broke 2 while clearing the holes:
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

This part here could be a bit wider:
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

This piece here could be wider or even not there at all:
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

This details here are difficult to print and borderline, any LED that's soldered a bit off will be an issue. Does it makes sense to have them?
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

This piece here could be wider or even not be there at all:
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

I see @philkry has by the photos the same board version as mine v1.0 and the extra height connector and he says everything fits perfectly which I find very strange?!

And a design challenge:
In order to change something attached to a screwed connector we would have to unscrew 5 screws, 1 of the cable holder and 4 for the cover.
What if the cover is not so pretty, so square but has cutouts so one could screw/unscrew without having to unscrew the hole cover?

philkry, 2020-11-01:
@joaobarros it could be my slicer settings that made it fit better for me as i was working with negative horizontal expansion to compensate for too narrow holes.

> This details here are difficult to print and borderline, any LED that's soldered a bit off will be an issue. Does it makes sense to have them?
i would say yes. at least the red led is helpful to see if CAN communication between the two boards works fine. it helped me quite a lot when assembling my printer.

>In order to change something attached to a screw connector we would have to unscrew 5 screws, 1 of the cable holder and 4 for the cover.
i agree, this is not ideal currently. it looks very nice but at the cost of practicality.
i would also favour a version which would expose the terminals, so we could access the screws without disassembling the entire thing.

joaobarros, 2020-11-01:
@philkry I understand what you're saying about the slicer settings but that doesn't explain the plug I show on the 1st picture, that's some 2mm at least of extra height.
I'd love to see a photo of that side on your print and Toolboard

pkucmus, 2020-11-01:
@joaobarros I made changes according to your (amazing) feedback, took a different approach with the bridge mount
https://cad.onshape.com/documents/255cffe335d549be4c0d4c52/w/027a43fe00d211ea4230f02e/e/795e637b64bf65caed4dccd1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

pkucmus, 2020-12-31:
Moving this to EVA 2 :)

Closed 2020-12-31.

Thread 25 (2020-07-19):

Sub assembly cart

pkucmus, 2020-07-19:
As a new EVA user I would like to have a page that would guide me through which sub assemblies are needed for my desired carriage so that EVA is more approachable to me.

The general idea is to have a page that will as questions like:
1. Which kinematics are you interested in?
2. Are you using MGN12 or MGN15?
3. Which extruder are you using?

After answering those questions an assembly is specified and with it all it's sub assemblies and parts (hardware or otherwise). The UI could work in a eCommerce cart fashion.

pkucmus, 2020-08-29:
After some thought I think I just need a sub assembly cart, one would add the sub assemblies needed to a cart of sorts and the in what would be a checkout view would aggregate all the parts that are required

pkucmus, 2020-12-31:
This is now redundant

Closed 2020-12-31.

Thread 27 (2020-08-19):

Compact Direct Drive / short filament path option

hernancurras, 2020-08-19:
Hey guys... I have been following the EVA project since long time ago. And to brainstorm EVA modular design, I would like to build/have a double geared compact option inspired on the Bondtech BMG Prusa Mk3 / MZ76v2 / Voron Afterburner 2.4 / CBRExtruder / ...

https://www.prusaprinters.org/es/prints/17584-bondtech-bmg-prusa-mk3smk25s-v2-fdm-printable-rhd-
http://vorondesign.com/voron2.4
https://github.com/AL3DAN/CBRExtruder

My personal taste, is build.in - self contained BMG dual geared + E3Dv6 + BLTouch.

Is it a feasible branch on EVA project?

pkucmus, 2020-08-20:
If I understand the idea I think I like it. Would give one the benefits of a BMG without the BMG (?).
With EVA I think there is an opportunity to do it "better" as in the fan is already taken care of and the motor can be on the back (saving Y space and moving the motor mass to the back). So it would boil down to making an EVA face I think.
That would be very nice.
All the source will be published with the next (1.3.0) release which is very close.

kuon, 2020-10-20:
Isn't the hemera a good option if you want a short filament path?

pkucmus, 2020-12-31:
Please move this Issue to EVA 2 https://github.com/EVA-3D/eva-main/issues if it's still something to desire :) (please also put the link to this issue there)

Closed 2020-12-31.

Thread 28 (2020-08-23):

MGH 12H carriage

cjeannerot25, 2020-08-23:
your project is for MGN 12C, it's possible to adapte for MGN 12H ?

pkucmus, 2020-08-24:
It's MGN15C and MGN12C to adapt to an H carriage one would just need to make a wider top part.

cjeannerot25, 2020-08-24:
even just changing the hole spacing it should be enough.  if you have the step files, I can make the modification in another branch

cjeannerot25, 2020-08-24:
I use direct drive stl, i can add a top part 😄

pkucmus, 2020-12-31:
Please move this Issue to EVA 2 https://github.com/EVA-3D/eva-main/issues if it's still something to desire :) (please also put the link to this issue there)

Closed 2020-12-31.

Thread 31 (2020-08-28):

Requesting a wersion that will allow to mount EVA on a Prusa/Reprap printer

Wellior0, 2020-08-28:

pkucmus, 2020-08-29:
Translated the title for international folk

pkucmus, 2020-12-31:
Please move this Issue to EVA 2 https://github.com/EVA-3D/eva-main/issues if it's still something to desire :) (please also put the link to this issue there)

Closed 2020-12-31.

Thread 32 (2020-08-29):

Use in BLV MGN 12

cjeannerot25, 2020-08-29:
I have a problem for use with BLV MGN, the connection part of the belt is reversed, it should be top right, and bottom left, currently on the EVA project it's reversed. I also use MGN12H and it's MGN12C on the EVA project (I redid the part for the BMG direct drive)

pkucmus, 2020-08-29:
BLV support was never tested, what if you'd mirror the back part? Not sure if the belts will align though

cjeannerot25, 2020-08-30:
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

I confirm belts is aligned ;)

cjeannerot25, 2020-08-30:
For back it's possible to connected 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

pkucmus, 2020-09-05:
Please see: https://cad.onshape.com/documents/1cea28d26150bba34a3d6614/v/0010d118035086ce95d3908d/e/8c43124770d234ffb36295f8 (notice configuration in top left) - far from being done since this only works for the V6 based variants but for BMG testing purposes should be ok

cjeannerot25, 2020-09-05:
No it's not possible to use in BLV mgn.

pkucmus, 2020-12-31:
Moved to EVA 2

Closed 2020-12-31.

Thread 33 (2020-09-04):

Tool changer

pkucmus, 2020-09-04:
For now the issue is here to brain storm ideas, any thoughts?

pkucmus, 2020-09-04:
Here's one idea involving a lead screw:
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

pkucmus, 2020-12-31:
I'm going to close this for now, but it will happen on EVA 2

Closed 2020-12-31.

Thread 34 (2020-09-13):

Dragon hotend support

pkucmus, 2020-09-13:
Seems like it's working out of the box :) At least dimension-wise (thank you Jonh D. for the pictures and testing!).
I'll leave the issue here in case there are more test results -stuff like: making sure nothing melts, is the air flow adequate, etc.

If there's anything to share in the topic please let me know here.

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

philkry, 2020-10-03:
@pkucmus i'm also using the dragon hotend but but my heater has issues keeping up the temperature.
it is stable until the part cooling fan turns on, then it goes down by 10-15° and never recovers.
i'm wondering if my heater is bad (brand new E3D high precision 30w) or if the fan duct somehow blows onto the heater cartridge?
did you experience something similar while testing? if not i will try replacing my heater.

pkucmus, 2020-10-03:
Horns duct is made not to blow directly on the nozzle or the heat block:
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
that said there is a lot of air being pushed everywhere - will bounce of the bed or the print, etc. 30W seems pretty weak (I'm using 50W ones), I had similar issues on different printers and 40W heaters, a silicone sock does a good job of isolating the cool air as well.
Before replacing your heater please run PID tuning and maybe PID tuning with the fan 100% PWM on - to teach it how to properly heat itself under those conditions.
I hope this helps.

philkry, 2020-10-03:
silicon sock is mounted already and the heater is also PID tuned with having part cooling at 100%.
i have a spare 40w heater here, will try this one and see if it improves. my first guess was just the horn duct, since i use the same heater model and part cooling fan on my Hemera extruder with super stable temperatures.

pkucmus, 2020-12-31:
Done in EVA 2.1.0: https://github.com/EVA-3D/eva-main/issues/5

Closed 2020-12-31.

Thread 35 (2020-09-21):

Angled duct printability issue

pkucmus, 2020-09-21:
The angled horn duct is angled so much that has a mid-air piece. Need to fix that. Thanks Pavel for reporting.

pkucmus, 2020-09-21:
Fix: https://cad.onshape.com/documents/d047f11e9330bd7b9dad92c7/w/41e36144e58664e1036c72a2/e/7ceece8903cd6a3e187d7937

pkucmus, 2020-09-21:
Pavel tested the angled version with Hemera, I'll test the other one soon.

pkucmus, 2020-12-31:
This one is solved (quite a while ago)

Closed 2020-12-31.

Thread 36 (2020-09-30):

Add information about Titan's groove mount.

pkucmus, 2020-09-30:
There is a part that is not described very well. While the groove mount is in theory not essential (since the PTFE tube can butt against the Titan's Filament guide) I did make a part for those that do not get the groove mount so describing it's usage is probably a good thing to do.

pkucmus, 2020-12-31:
Done in EVA 2

Closed 2020-12-31.

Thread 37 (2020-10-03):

Idex version fan mount is too fragile

kuon, 2020-10-03:
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

The highlighted element is quite fragile and should be made thicker.

pkucmus, 2020-10-03:
I have thicken the "hooks" by 1mm each, for IDEX and Cartesian Backs, please see: https://cad.onshape.com/documents/1cea28d26150bba34a3d6614/w/fd185c58d38d06bda7ec83a6/e/8d4e73fd9c11258ba0412b03

kuon, 2020-10-03:
Yeah, that should do it.

kuon, 2020-10-06:
There is another issue with those two hooks, they are separated by 15.2mm, but my fans are 15.25mm. I looked at different fan datasheets, and the tolerance is between 0.25mm and 0.5mm, so I suggest we change this width to 15.5mm instead of 15.2mm.

pkucmus, 2020-10-07:
Done, please let me know what you think: https://cad.onshape.com/documents/1cea28d26150bba34a3d6614/w/fd185c58d38d06bda7ec83a6/e/8d4e73fd9c11258ba0412b03

kuon, 2020-10-07:
Yeah, looks good to me.

Closed 2020-10-07.

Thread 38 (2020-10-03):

V6 face front bottom is really thin

kuon, 2020-10-03:
The V6 front has a really thin part at the bottom (selected face), would it be possible to make it a bit thicker?

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

pkucmus, 2020-10-03:
I reduced the revolve angle on the V6 face - now it does not cut into the thin bottom face, please check: https://cad.onshape.com/documents/1cea28d26150bba34a3d6614/w/fd185c58d38d06bda7ec83a6/e/8c43124770d234ffb36295f8

kuon, 2020-10-03:
I have not printed it yet, but it is better in the slicer. It looks like it is ok, I'll reopen if it's still too thin after printing.

Closed 2020-10-03.

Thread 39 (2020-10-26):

Aero face modelling glitches

mpeto, 2020-10-26:
Extrude 49 - protrudes on the other side - esthetic issue
Extrude 41 - wrong profile selection, hexagon's inscribed circle smaller than original hole's counterbore diameter (same issue with all faces with nut sockets)
Chamfer 26 leaves a small gap at the intersection with the motor mounting face

pkucmus, 2020-11-22:
I lost the CAD link from you, can you provide me one? Or the STEP file

mpeto, 2020-11-23:
I think this was it:
https://cad.onshape.com/documents/00da96811a434ceb4ebdf5e1/w/e6de0b894be33ca234b23969/e/79c5b4f601dfed4a447bd261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
Onshape<https://cad.onshape.com/documents/00da96811a434ceb4ebdf5e1/w/e6de0b894be33ca234b23969/e/79c5b4f601dfed4a447bd261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>
Login / Signin to Onshape - the modern CAD system used by thousands of companies worldwide.
cad.onshape.com

________________________________
Feladó: Paweł Kucmus <notifications@github.com>
Elküldve: 2020. november 22., vasárnap 16:16
Címzett: pkucmus/EVA <EVA@noreply.github.com>
Másolatot kap: mpeto <matyas.peto@hotmail.com>; Author <author@noreply.github.com>
Tárgy: Re: [pkucmus/EVA] Aero face modelling glitches (#39)

I lost the CAD link from you, can you provide me one? Or the STEP file

—
You are receiving this because you authored the thread.
Reply to this email directly, view it on GitHub<https://github.com/pkucmus/EVA/issues/39#issuecomment-731763241>, or unsubscribe<https://github.com/notifications/unsubscribe-auth/ARQQ2765EL55RH7NGIWCA33SRETM7ANCNFSM4S7FF4DA>.

pkucmus, 2020-12-31:
Aero was remade in EVA 2. Please feel free to comment and recommend improvements https://github.com/EVA-3D/eva-main/issues

Closed 2020-12-31.

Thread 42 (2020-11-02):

Request for 2 in 1 / ZSYong mix hotend

manuelchaves, 2020-11-02:
Request for 2 in 1 / ZSYong mix hotends, two color mix plz. TKS
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

https://pt.aliexpress.com/item/4000145873157.html
https://pt.aliexpress.com/item/4000293113610.html

EduardoOliveira, 2020-11-02:
Is that height compatible with the non mixing one?

pkucmus, 2020-12-31:
Please move this Issue to EVA 2 https://github.com/EVA-3D/eva-main/issues if it's still something to desire :) (please also put the link to this issue there)

Closed 2020-12-31.

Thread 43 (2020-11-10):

Top part only for MGN12C

alessg1, 2020-11-10:
Your top part is only design for MGN12c witch have 15mm x 20mm distance between holes.
You shoud also make version for MGN12H witch have 20mm x 20mm

EduardoOliveira, 2020-11-10:
Wich top part do you need? I've edited the tops and printed the BMG, I know the bowden top is also ok, not sure about the other one, I can share if you like. Mng12h

alessg1, 2020-11-10:
I already modify BGM top to be compatible with MGN12H. But now i need to modify bottom one to be compatible with BLV mgn cube endstop

pkucmus, 2020-12-31:
Please move this Issue to EVA 2 https://github.com/EVA-3D/eva-main/issues if it's still something to desire :) (please also put the link to this issue there)

Closed 2020-12-31.

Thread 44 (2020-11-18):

[EVA 2.0] Anchor points for zip ties

joaobarros, 2020-11-18:
On EVA version 1.x there where anchor points for zip ties on the Back and I added one on the bottom as can be seen on the following picture:
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

Of course this is desirable in EVA 2.0 as well so I propose anchor points as marked with red rectangles:
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

pkucmus, 2020-12-31:
Done in EVA 2 - thanks for pushing for it @joaobarros - it's an awesome improvement

Closed 2020-12-31.

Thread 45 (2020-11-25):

Adjust bl touch mount for DIN 912 screw

kuon, 2020-11-25:
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

To be able to mount the bl touch mount with DIN 912 screw, there should be at least 3mm for the head (only 1mm now).

Here is my modified version (I drilled the part afterward, so it's a bit too deep.)

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

pkucmus, 2020-12-31:
This changed in EVA 2 https://github.com/EVA-3D/eva-main please check it out

Closed 2020-12-31.

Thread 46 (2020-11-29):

Mosquito front question

maziggy, 2020-11-29:
I'm currently assembling the latest Mosquito version and wondering if the small PTFE tube should go also through the front part?

https://github.com/pkucmus/EVA/blob/master/docs/media/stls/mosquito_front.stl

If so, then the hole is too small.

Thanks, Martin

miklschmidt, 2020-11-29:
Your PTFE tube shouldn't be thicker than 4mm, the hole is 4.2mm, so it should go through without issues. Have you calibrated your flow?

pkucmus, 2020-12-31:
This changed in EVA 2 https://github.com/EVA-3D/eva-main please check it out

Closed 2020-12-31.

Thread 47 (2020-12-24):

Titan v6 front question

LucidityCrash, 2020-12-24:
Why does this not place the v6 hotend inside the Titan but clamp it outside lower down ?  This makes no sense you've essentially increased the filament path length making giving it all the issues of a bowden extruder but not the advantage of less moving mass.  It also increases the height of the assembly meaning a reduced Z build volume.

pkucmus, 2020-12-25:
It's hard to answer a "why it's done that way" question... There are many reasons and factors in which had be considered:

1. EVA is about being modular - the extra space often asks as a compatibility layer between different variants and permutations
2. Moving the tip of the nozzle as high for it to go into titans groove mount would make the nozzle be only 0.4mm bellow the 2020 - not an option
3. I wanted the motor (the heaviest part) to be as close to the center of the carriage as possible - that defines where the motor is and where the titan is.
4. I also wanted to have the layer cooling duct not obstructing the view of the nozzle - which either meant having the duct come from bellow of the top, bellow was better for easier parts (to design, maintain and print)
5. **24.7 mm added filament path** (in the case of titan and V6) has very little to do with a hundreds of mm long bowden tube, I was using EVA Titan for the longest time and those extra mm never bothered me.
6. The build volume of for e.g. Rat Rig V-core Pro printer was increased or at least did not change

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

LucidityCrash, 2020-12-26:
Understood ... You could have done what you did for the Aero, which is essentially the same but even shorter and rotate the motor by 90 Degrees and place it in front of the profile.  Obviously this violates point 3 :)

Do/Did you use the groove mount bowden adaptor or just run the tube straight up into the black plastic part inside the titan.

Out of interest what did you change to after the Titan ... I'm in the process of upgrading my Prusa i3 to the RatRig V-Core Pro and originally I was going to take the extruder/hotend off but now I'm thinking I'm going to get a new one for the new printer.  The Hemera looked good but is sold out ... was thinking of going with the Aero.

pkucmus, 2020-12-26:
You don't need the groove mount, the PTFE has a place to "lock" itself in place inside the white, slippery part of Titan. But I made a printable one in case someone would still opt to use one.

I got a BMG from the community so I'm using that on my main V-core 3, my V-core Pro will get a Dragon + Titan. But It have no need for the short path ones like Aero or Hemera (those two are also front heavy and steal from of the build space). If you have a Titan I'd try that - you may end up being perfectly happy with it.

There's also an idea to make a short path. Prusa MK3-like EVA face with dual gear extrusion but that's in the future.

pkucmus, 2020-12-31:
I'm assuming there's not much to discuss here. Closing, thanks!

Closed 2020-12-31.

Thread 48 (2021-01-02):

EVA 2.1: BLtouch hits the idler while homing

top-gun, 2021-01-02:
My v core pro 1.2 uses the original idlers from Easymod 1.1, the xy joiners from Easymod 1.2 and the EVA 2.1 carriage. A bltouch 3.1 is mounted.

When homing, the printer homes first x, then y. In that sequence, the bltouch hits the idler right before Y reaches 0.

i added a t nut and a 5mm bolt t limit the y driveway, sacrificing about 10mm of buildspace in Y.

Closed 2021-03-19.

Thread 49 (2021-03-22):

Current duct too close to Mosquito and Dragon Heat Blocks

bionicmunky, 2021-03-22:
The current cooling duct is susceptible to warping on the side where the wires for the heater come out.

Per the comment in the EVA channel on Discord, it would be great if a variant with a wider gap between left right (2-4mm) would be welcomed. Slight lower (1mm)  might also be helpful.

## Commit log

2020-04-23 add first files
    [Backs - Back with Tensioning.stl, Bottoms - Base.stl, Bottoms - Straight.stl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]
2020-04-24 Add Titan press fit adapter
    [Titan press fit adapter.stl]
2020-04-25 Small tweaks to the Hemera carriage, add hemera doc
    [Faces - Hemera Front.stl, Faces - Hemera Probe Front.stl, Faces - Hemera.stl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]
2020-04-30 Add the Aero carriage, bl-touch probe mounts, hemera alt probe mount and 12mm inductive probe mount, fixes #2, #3, #4, #5
    [Bl-touch - BL-Touch (thick).stl, Bl-touch - BL-Touch.stl, Bottoms - Aero.stl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]
2020-05-03 Fix the back plate to allow screws from the back
    [Backs - Back with Tensioning.stl]
2020-05-07 Add a 9mm tension slider that has differently oriented teeth for non V-core printes
    [Dynamic - Slider.stl]
2020-05-10 Add multi degree backs, add different tension sliders, reorganize directories
    [All Backs (for export) - back_cartesian_30deg.stl, All Backs (for export) - back_cartesian_45deg.stl, All Backs (for export) - back_cartesian_60deg.stl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]
2020-05-10 change documentation, remove wiki, rename files
    [All Backs (for export) - back_cartesian_30deg.stl, All Backs (for export) - back_cartesian_45deg.stl, All Backs (for export) - back_cartesian_60deg.stl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]
2020-05-10 create the documentation page
    [bottom_14mm_duct.stl]
2020-05-11 Fix the broken M5 tension sliders
    [tension_slider_9mm_belt_M5.stl, tension_slider_9mm_belt_M5_flip.stl]
2020-05-29 Add horn ducts that are raised by 1mm for less tolerant printers
2020-06-06 The main feature of this release is the support for MGN12 rails. It also addresses some feature requests and issues mainly around less fine tuned printers:
    1. The tension sliders are more tolerant - should fit easier into their pockets.
    2. A 6mm belt square M3 nut variant of the cartesian tension slider was added.
    3. The 6mm belt M3 slider was improved.
    4. Both fan ducts now have a "risen" variant that moves the duct horns 1mm highier.
    5. V6 titan top piece had it's cable mount moved to allo for bigger motors.
    6. Endstop spacers were added to allow easier endstop mounting on the BMG and Titan variants.
    7. The cartesian back has a different belt grip for easier assembly (the previous one was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
    [12mm endstop spacer.stl, 6mm endstop spacer.stl, back_cartesian_30deg.stl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]
2020-07-19 Fix BOM counting script
2020-08-28 Idex support
    - **Add IDEX back parts** - EVA now supports IDEX kinematics!
    - **Change Cartesian back** - it's not a neglected part anymore
    - **Add Cartesian cable holder**
    - **Simplify tops** - there are only two types of the top part
    - **Deprecated Hemera** - The "alternative" solution was picked as the better one by the users, since the effort to keep them both was bigger than the gain I got rid of the less popular one (you can 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
    - **Add new cable holder standard** - the backs now have a standard mount for the new cable mounts
    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
    [back_cartesian.stl, back_cartesian_30deg.stl, back_cartesian_45deg.stl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]
2020-08-29 Add a few screws to the bom, add table sorting
2020-10-31 Remove the old docs builder, use a pre-built site
    [12mm endstop spacer.stl, 6mm endstop spacer.stl, back_cartesian.stl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]
2020-10-31 fix broken img url in assembly list
2020-10-31 add forgotten IDEX, probes, sliders
    [Back_IDEX_-_back_idex_x1.stl, Back_IDEX_-_back_idex_x2.stl, probes - bl_touch.stl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]
2021-02-18 Add info about deprecation
    [Back_IDEX_-_back_idex_x1.stl, Back_IDEX_-_back_idex_x2.stl, back_cartesian.stl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]
